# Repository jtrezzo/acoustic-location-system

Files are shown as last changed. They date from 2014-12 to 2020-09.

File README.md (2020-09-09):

acoustic-location-system
========================

Software and hardware designs for an acoustic location system suitable for small underwater ROVs such as OpenROV

This project is about developing an acoustic based location system for small ROVs.

Much of the early work that we have been doing is in the blog: https://forum.openrov.com/t/acoustic-modems-location-and-pingers
That blog covers broader topics, so I wanted to start a forum discussion specifically for developing the acoustic location system.  https://forum.openrov.com/t/acoustic-location-system

Knowing where you are when exploring and gathering images and data is clearly a vital piece of information.  GPS systems provide this on land.  Underwater, radio waves that GPS depends on to function are absorbed by water.  Acoustic signals are one of the best alternatives to transmit information for location and other data communication.  Commercial underwater modem systems exist today and are widely used in exploration, but suitable systems for low-cost small size platforms like OpenROV are not available.  This project plans to deliver such a system and is in-part inspired by university research in this area – Bridget Benson’s UCSD PhD Thesis http://haduken.ucsd.edu/papers/phd-thesis-benson.pdf is one example.
Information about 3D location in real-time is a key enabler for many scientific and exploratory needs. The technology to do this is known, but has not been scaled down for systems of this size. With location information, one could map any discoveries (sunken ships, archeological sites, and coral reefs are some examples). Maps of the ocean/lake/cave can be made with location and sensor information together. Virtual Reality and 3D gaming technology could be used to represent information about an exploration either in real-time (shared over the internet) or archived for many to explore on-line as they study results of explorations.
The technical approach is to use acoustic transmissions (ultrasonic sonar) from known locations on the surface (GPS would be used to maintain location of the sender). The ROV would have a receiver unit on board and can determine the time for the signal to arrive. That information along with depth, temperature and the on-board IMU (gyro, compass, accelerometers) would be used to determine/compute location. Location information would be available to the operator of the ROV and a graphical display could be developed (possibly in conjunction with maps of the bottom if available) to help with navigation.

Current status and near term work items:
Working designs for ultrasonic Power AMP and receiver exist and initial testing with 40KHz piezoelectric transducers has begun.  A micro-controller or processor can be used to generate a 40KHz square wave pulse which is shaped and amplified into a sine wave to drive the transducer.  Currently the amplifier produces a 27Vp-p signal.  If testing shows that this is not enough to generate a powerful enough ultrasonic pulse, a step-up transformer may be required.
The high gain (> 100), high input impedance (FET front end) receiver amplifier design includes a narrow band pass filter to allow only frequencies in the desired range to be amplified.  This receiver needs to be packaged and integrated with the ROV electronics along with a micro-controller to process the waveform (>100 samples/sec and real-time FFT processing required).  
System level: Some how the timing for the start of the pulse from each transmitter (correlated with GPS location at time of transmission) must be matched against the time the first pulse is received (any delayed echoes would be rejected).  The time of travel for the pulse would be used to calculate the distance from the transmitter (with know location) and along with depth information, water temperature, salinity (salt or fresh) and IMU data (plus and location history - dead reckoning, etc.) location would be determined. Data from a second transmitter some distance from the first would greatly help the calculation (see Virtual Long Baseline VLBL Navigation).  The transmissions and calculations should be able to be done every tenth of a second to provide timely location.
I will establish a location on GitHub for this project and start to organize existing material there.  for now, take a look at the blog https://forum.openrov.com/t/acoustic-modems-location-and-pingers.
It would speed things up if I got some help with the micro-controller software while I continue with the electronics and in the water testing.  To do: sample the signal and determine when a 40KHz pulse arrives.  Digital signal processing (DSP) analysis would be the likely approach.  Also will need to determine which micro-controller is adequate to handle this processing load.  I will collect some raw data samples using my NI VirtualBench if someone just wants to work on the DSP part.
There are a few folks already interested, and some possibility of collaboration is there.
If you are interested in getting involved, please let me know and what area(s) you think you can hep with.

I have added a folder with results from acoustic testing.  It includes the results of some initial DSP processing using MATLAB, courtesy of Frikk Solberg of Norway.

Regards,

Jim Trezzo
jtrezzo@trezco.com

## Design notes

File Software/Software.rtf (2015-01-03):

Software folder

TonePulse - simple program to generate pulse of square waves at 40KHz and send digital trigger to data acquisition program (start collecting points). The trigger will be sent down the tether to the micro controller on the ROV. The square wave will be input to the ultrasonic transmitter that drives the transducer. This software will be modified to read the GPS data from a USB GPS device and record time and location when pulse is sent.

adcspeedtest (3.1 and 3.2) - using Teensy 3.1 micro controller, can sample signal at > 250K samples per second. adcspeedtest3.1 uses ADC library (ADC-master) from the Teensy website and collects as many points as can fit into memory. adcspeedtest3.2 uses built in library for Teensy. It only stores 500 points (can be modified to many more) and is triggered by a digital I/O. Both programs are test software for collecting signal data remotely using a micro controller. The plan is to put the analog receiver and Teensy 3.1 into the e-chassis on the ROV and interface with the BBB using the serial port. The transducer will be attached to the ROV and connected to a pair of wires that go into the e-chassis. The analog ultrasonic amplifier will be connected to the ADC on the Teensy. I need to modify the circuit to provide a DC bias and over-voltage protection (ADC only goes from 0-3.3V, the signal is 40KHz AC)

After each cycle of points collection the adcspeedtest program outputs the results as CSV data to the serial port. I then cut and past the results into a text file for processing.

PythonProgram - First cut at reading results from points collection into a graph. This software can evolve to do some DSP analysis. Once the algorithms are figured out (to measure the time for the acoustic pulse to arrive) this can be implemented on the micro controller and time-stamped results can be sent to the BBB (as a JSON string). The OpenROV Node.js software (via a plugin) can send the results as part of the socket.io data stream to software on the surface which can do the calculation for location (surface transmitter has GPS location and time pulse was sent).

First phase of this experiment is to acquire points data from on-board the ROV and modify electronics and software based on observations.

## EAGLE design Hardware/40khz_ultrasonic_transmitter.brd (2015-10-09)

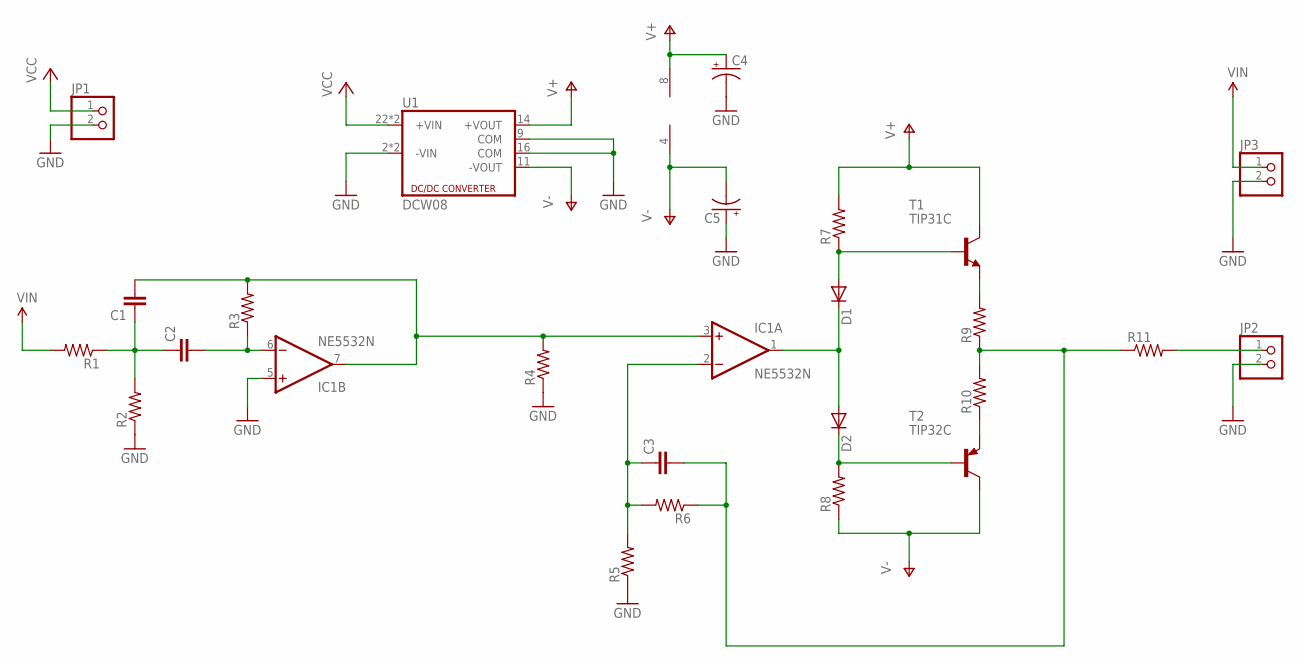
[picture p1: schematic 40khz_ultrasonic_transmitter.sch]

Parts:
C1, C2, C3: CAPPTH2; CAP-PTH-SMALL2
C4, C5: CAP_POLPTH1; CPOL-RADIAL-100UF-25V
D1, D2: DIODE1N4148; DIODE-1N4148
IC1: NE5532N; DIL08
JP1, JP2, JP3: PINHD-1X2; 1X02
R1, R2, R3, R4, R5, R6, R7, R8, R9, R10: RESISTORPTH-1/4W; AXIAL-0.4
R11: RESISTORPTH-2W; AXIAL-0.8
T1: TIP31C; TO220
T2: TIP32C; TO220
U1: DCW08

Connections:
GND: C4.2 (-), C5.1 (+), IC1.5 (+IN), JP1.2, JP2.2, JP3.2, R2.P$1 (1), R4.P$1 (1), R5.P$1 (1), U1.2 (-VIN), U1.3 (-VIN), U1.9 (COM), U1.16 (COM)
unnamed: C3.2, R6.P$1 (1), R9.P$1 (1), R10.P$2 (2), R11.P$1 (1)
unnamed: R9.P$2 (2), T1.3 (E)
unnamed: R10.P$1 (1), T2.3 (E)
unnamed: D1.A, R7.P$1 (1), T1.1 (B)
unnamed: D2.C, R8.P$2 (2), T2.1 (B)
unnamed: C1.2, IC1.3 (+IN), IC1.7 (OUT), R3.P$2 (2), R4.P$2 (2)
unnamed: C1.1, C2.1, R1.P$1 (1), R2.P$2 (2)
unnamed: C3.1, IC1.2 (-IN), R5.P$2 (2), R6.P$2 (2)
unnamed: C2.2, IC1.6 (-IN), R3.P$1 (1)
unnamed: JP2.1, R11.P$2 (2)
unnamed: D1.C, D2.A, IC1.1 (OUT)
V+: C4.1 (+), IC1.8 (V+), R7.P$2 (2), T1.2 (C), U1.14 (+VOUT)
V-: C5.2 (-), IC1.4 (V-), R8.P$1 (1), T2.2 (C), U1.11 (-VOUT)
VCC: JP1.1, U1.22 (+VIN), U1.23 (+VIN)
VIN: JP3.1, R1.P$2 (2)

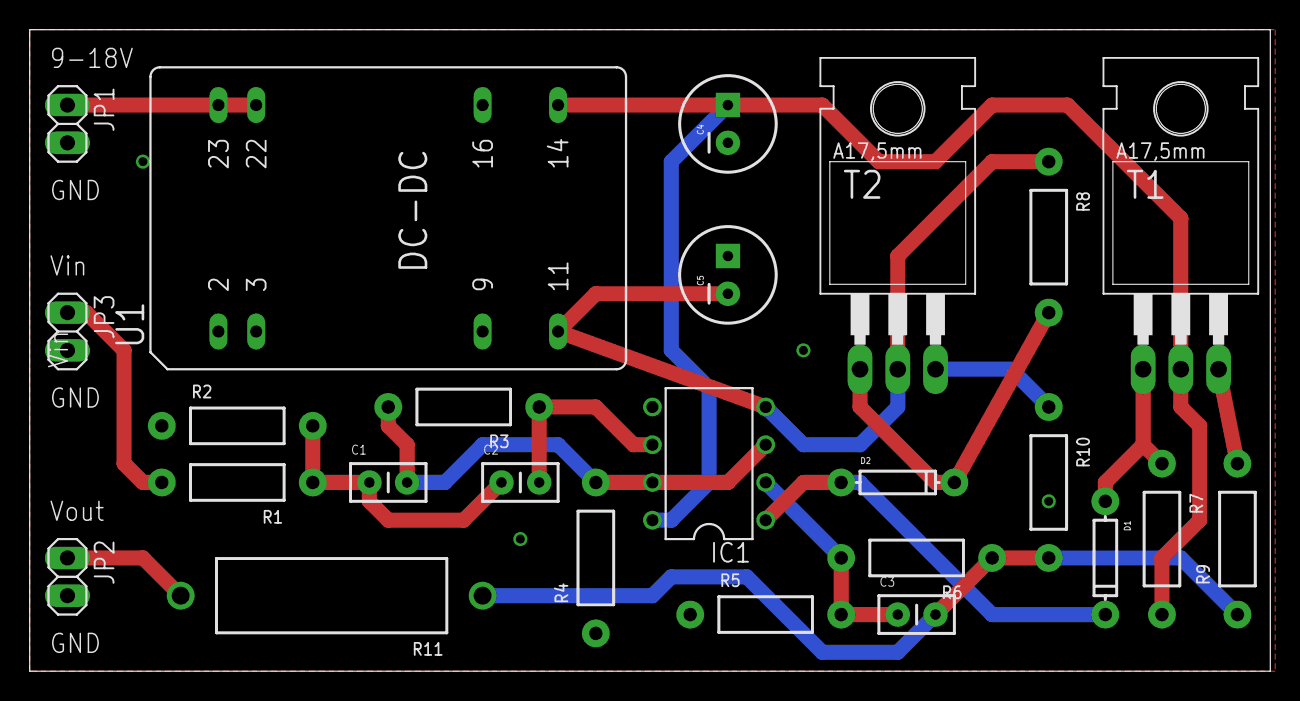
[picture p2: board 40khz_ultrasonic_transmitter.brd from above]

Board: 2 copper layers, 83.5 x 43.2 mm, 25 parts (0 on the bottom side), 16 nets.

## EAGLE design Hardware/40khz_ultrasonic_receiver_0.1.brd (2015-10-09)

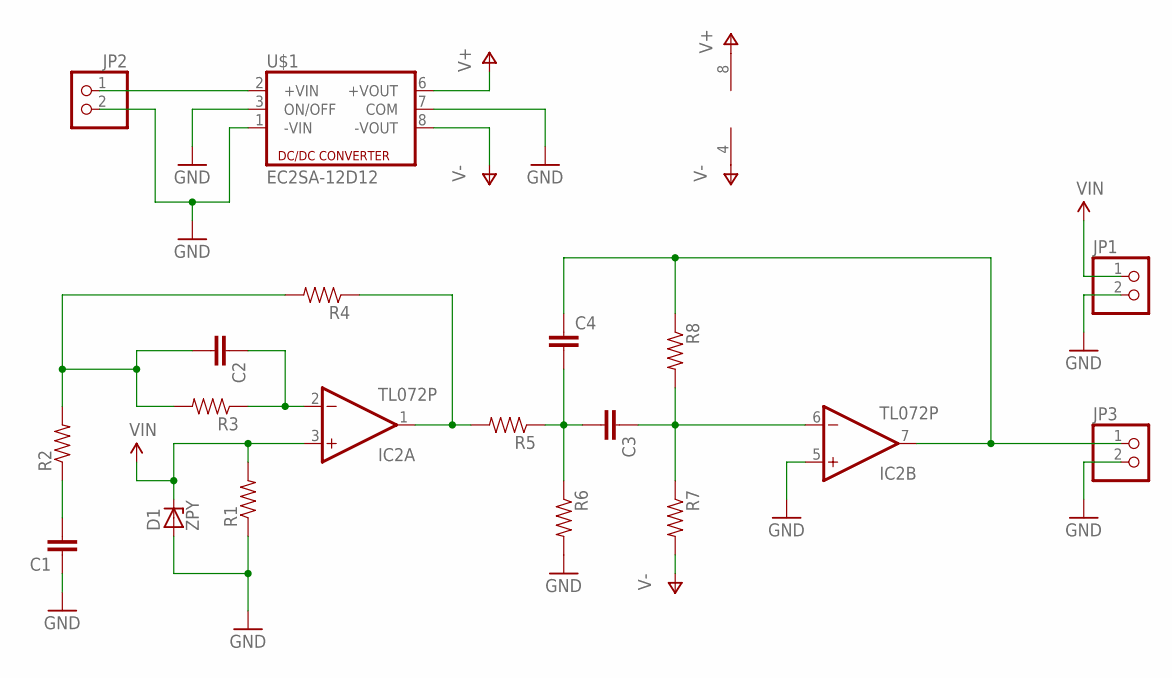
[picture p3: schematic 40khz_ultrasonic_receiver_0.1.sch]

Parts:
C1, C2, C3, C4: CAPPTH; CAP-PTH-SMALL
D1: ZPY; DO41Z10
IC2: TL072P; DIL08
JP1, JP2, JP3: PINHD-1X2; 1X02
R1, R2, R3, R4, R5, R6, R7, R8: RESISTORPTH-1/4W; AXIAL-0.4
U$1: EC2SA-12D12; EC2SA

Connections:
GND: C1.1, D1.A, IC2.5 (+IN), JP1.2, JP2.2, JP3.2, R1.P$1 (1), R6.P$2 (2), U$1.1 (-VIN), U$1.3 (ON/OFF), U$1.7 (COM)
unnamed: IC2.1 (OUT), R4.P$1 (1), R5.P$2 (2)
unnamed: C3.2, C4.2, R5.P$1 (1), R6.P$1 (1)
unnamed: C2.1, IC2.2 (-IN), R3.P$1 (1)
unnamed: C4.1, IC2.7 (OUT), JP3.1, R8.P$1 (1)
unnamed: C2.2, R2.P$2 (2), R3.P$2 (2), R4.P$2 (2)
unnamed: C3.1, IC2.6 (-IN), R7.P$1 (1), R8.P$2 (2)
unnamed: C1.2, R2.P$1 (1)
unnamed: JP2.1, U$1.2 (+VIN)
V+: IC2.8 (V+), U$1.6 (+VOUT)
V-: IC2.4 (V-), R7.P$2 (2), U$1.8 (-VOUT)
VIN: D1.C, IC2.3 (+IN), JP1.1, R1.P$2 (2)

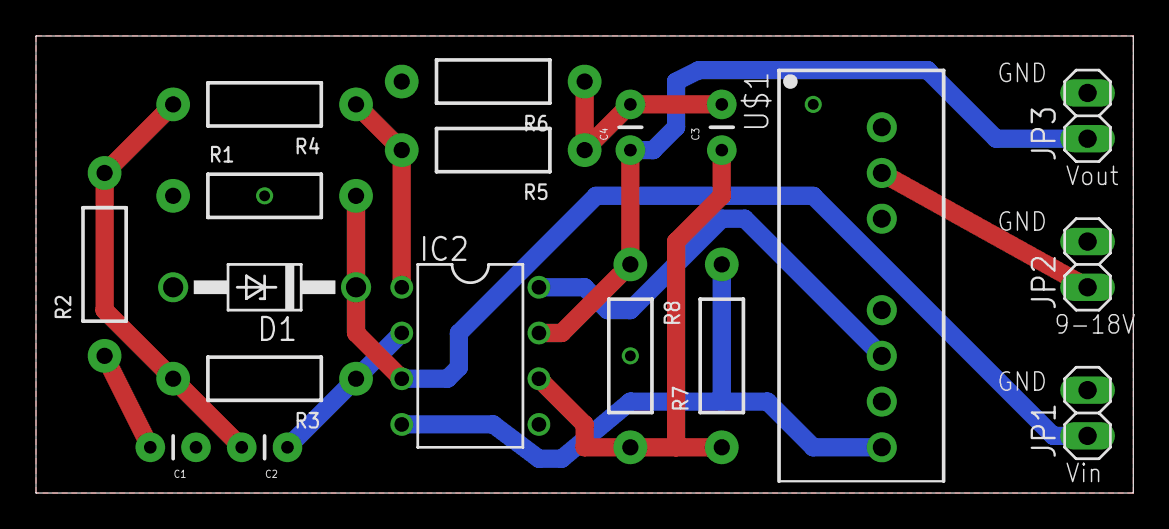
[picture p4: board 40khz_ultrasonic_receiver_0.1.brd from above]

Board: 2 copper layers, 61.0 x 25.4 mm, 18 parts (0 on the bottom side), 12 nets.

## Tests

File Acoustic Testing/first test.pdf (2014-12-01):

First Test of sonar detection algorithm

Here are the first results from the algorithm I have tested. It is quite simple and uses a couple of steps on the received signal

1. Absolute value of received signal
2. Low pass filter it to create an envelope with cutoff frequency at 20kHz
3. Create threshold by finding the average of the signal
4. Find first point where the signal value is larger than the threshold

The filtering procedure works well, but the threshold is not good enough yet. Just averaging is obviously not good enough. I will try to look into some other thresholding methods soon and see what I can do. Underneath are the plots for 0.5m, 1m, 2m, 3m and 4m depth respectively. If it is hard to see, on each figure, the first plot is the sent signal and the second is the received(Or that is what I assume). The third on has the absolute valued version of the received signal in blue, in red is the envelope and the threshold is in green.

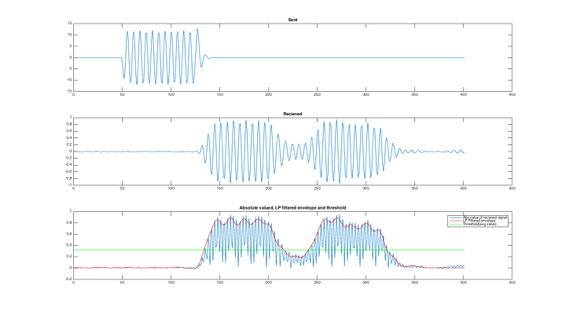
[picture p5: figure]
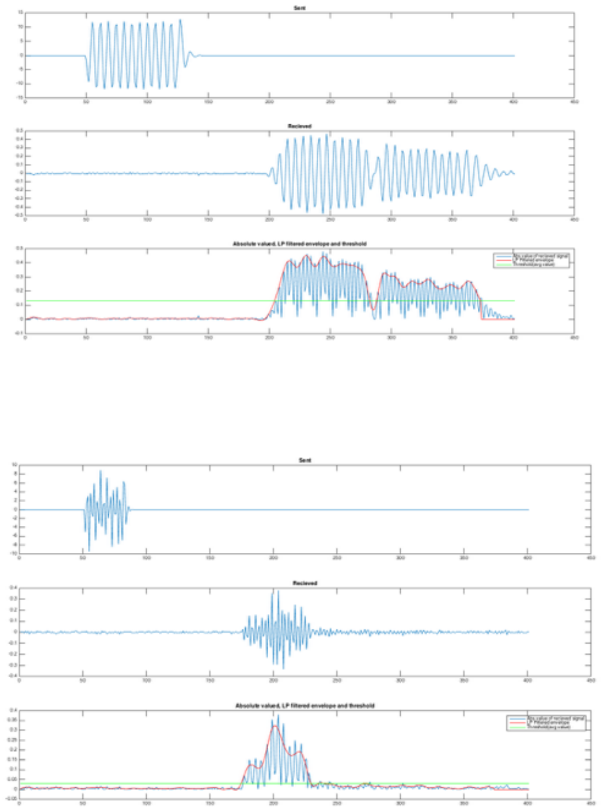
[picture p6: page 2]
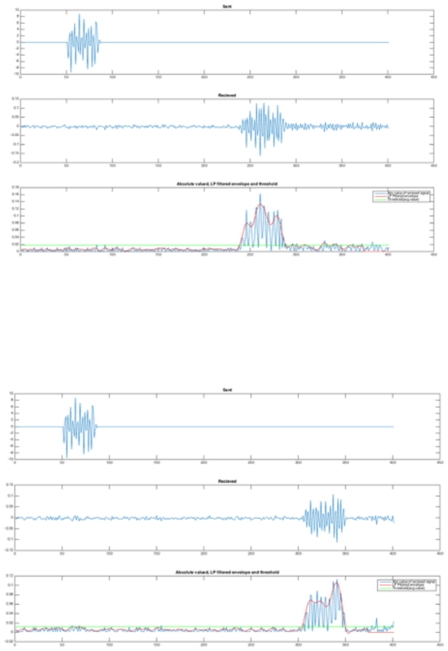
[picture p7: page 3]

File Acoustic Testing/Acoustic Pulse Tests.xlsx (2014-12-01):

Acoustic Pulse Testing |  | 2014-11-06
Distance in Meters | Voltage in mV | Delay in mSec | Meters/Sec
1 | 1860 | 0.68 | 1470.588235
2 | 2290 | 1.35 | 1481.481481
3 | 675 | 2 | 1500
4 | 733 | 2.7 | 1481.481481

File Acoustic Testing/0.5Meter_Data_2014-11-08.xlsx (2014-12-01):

NI VB-8012
Configuration
 | Device
 |  | Name | Serial Number | Firmware
 |  | VB8012-306042E | 306042E | 1.0.1f0
MIXED SIGNAL OSCILLOSCOPE |  |  |  |  |  |  |  |  |  |  |  |  |  |  |  |  |  |  | DC POWER SUPPLY |  |  |  |  |  | DIGITAL MULTIMETER |  |  |  |  |  |  | DIGITAL I/O
Configuration |  |  |  |  |  |  |  |  |  |  |  |  |  |  |  |  |  |  | Configuration |  |  |  |  |  | Configuration |  |  |  |  |  |  | Configuration
 | Analog |  |  |  |  |  |  |  | Trigger |  |  |  |  |  |  |  | Acquisition |  |  | Analog |  |  |  |  |  | Analog |  |  |  |  |  |  | Digital
 |  | Name | Alias | Channel Coupling | Probe Attenuation | Volts Per Division | Vertical Offset (V) | ŒîT (ns) |  | Type | Delay (s) | Reason | Edge | Source | Level (V) | Hysteresis |  | Mode |  |  | Name | Operating Mode | Voltage Set Point | Amperage Set Point |  |  | Name | Measurement Mode | Measurement Range | Input Impedance | Null Offset |  |  | Name | Direction
 |  | 1 | 1 | DC | 1X | 500 mV/ | 0.952537 | 4008 |  | Edge | -2.8e-05 | Triggered | Rising | 2 | 0 | Minimum |  | Peak Detect |  |  | +6 V | CV | 0 | 1 |  |  | DMM | VDC | 100 mV | Normal Impedance (10 MŒ©) | Off |  |  | 0 | Input
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

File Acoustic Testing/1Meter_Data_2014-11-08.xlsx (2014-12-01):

NI VB-8012
Configuration
 | Device
 |  | Name | Serial Number | Firmware
 |  | VB8012-306042E | 306042E | 1.0.1f0
MIXED SIGNAL OSCILLOSCOPE |  |  |  |  |  |  |  |  |  |  |  |  |  |  |  |  |  |  | DC POWER SUPPLY |  |  |  |  |  | DIGITAL MULTIMETER |  |  |  |  |  |  | DIGITAL I/O
Configuration |  |  |  |  |  |  |  |  |  |  |  |  |  |  |  |  |  |  | Configuration |  |  |  |  |  | Configuration |  |  |  |  |  |  | Configuration
 | Analog |  |  |  |  |  |  |  | Trigger |  |  |  |  |  |  |  | Acquisition |  |  | Analog |  |  |  |  |  | Analog |  |  |  |  |  |  | Digital
 |  | Name | Alias | Channel Coupling | Probe Attenuation | Volts Per Division | Vertical Offset (V) | ŒîT (ns) |  | Type | Delay (s) | Reason | Edge | Source | Level (V) | Hysteresis |  | Mode |  |  | Name | Operating Mode | Voltage Set Point | Amperage Set Point |  |  | Name | Measurement Mode | Measurement Range | Input Impedance | Null Offset |  |  | Name | Direction
 |  | 1 | 1 | DC | 1X | 500 mV/ | 1.006228 | 4008 |  | Edge | -2.8e-05 | Triggered | Rising | 2 | 0 | Minimum |  | Peak Detect |  |  | +6 V | CV | 0 | 1 |  |  | DMM | VDC | 100 mV | Normal Impedance (10 MŒ©) | Off |  |  | 0 | Input
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

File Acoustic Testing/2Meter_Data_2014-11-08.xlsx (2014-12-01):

NI VB-8012
Configuration
 | Device
 |  | Name | Serial Number | Firmware
 |  | VB8012-306042E | 306042E | 1.0.1f0
MIXED SIGNAL OSCILLOSCOPE |  |  |  |  |  |  |  |  |  |  |  |  |  |  |  |  |  |  | DC POWER SUPPLY |  |  |  |  |  | DIGITAL MULTIMETER |  |  |  |  |  |  | DIGITAL I/O
Configuration |  |  |  |  |  |  |  |  |  |  |  |  |  |  |  |  |  |  | Configuration |  |  |  |  |  | Configuration |  |  |  |  |  |  | Configuration
 | Analog |  |  |  |  |  |  |  | Trigger |  |  |  |  |  |  |  | Acquisition |  |  | Analog |  |  |  |  |  | Analog |  |  |  |  |  |  | Digital
 |  | Name | Alias | Channel Coupling | Probe Attenuation | Volts Per Division | Vertical Offset (V) | ŒîT (ns) |  | Type | Delay (s) | Reason | Edge | Source | Level (V) | Hysteresis |  | Mode |  |  | Name | Operating Mode | Voltage Set Point | Amperage Set Point |  |  | Name | Measurement Mode | Measurement Range | Input Impedance | Null Offset |  |  | Name | Direction
 |  | 1 | 1 | DC | 1X | 500 mV/ | 0.952537 | 10048 |  | Edge | 0.00087 | Triggered | Rising | 2 | 0 | Minimum |  | Peak Detect |  |  | +6 V | CV | 0 | 1 |  |  | DMM | VDC | 100 mV | Normal Impedance (10 MŒ©) | Off |  |  | 0 | Input
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

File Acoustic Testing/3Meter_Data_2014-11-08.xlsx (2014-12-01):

NI VB-8012
Configuration
 | Device
 |  | Name | Serial Number | Firmware
 |  | VB8012-306042E | 306042E | 1.0.1f0
MIXED SIGNAL OSCILLOSCOPE |  |  |  |  |  |  |  |  |  |  |  |  |  |  |  |  |  |  | DC POWER SUPPLY |  |  |  |  |  | DIGITAL MULTIMETER |  |  |  |  |  |  | DIGITAL I/O
Configuration |  |  |  |  |  |  |  |  |  |  |  |  |  |  |  |  |  |  | Configuration |  |  |  |  |  | Configuration |  |  |  |  |  |  | Configuration
 | Analog |  |  |  |  |  |  |  | Trigger |  |  |  |  |  |  |  | Acquisition |  |  | Analog |  |  |  |  |  | Analog |  |  |  |  |  |  | Digital
 |  | Name | Alias | Channel Coupling | Probe Attenuation | Volts Per Division | Vertical Offset (V) | ŒîT (ns) |  | Type | Delay (s) | Reason | Edge | Source | Level (V) | Hysteresis |  | Mode |  |  | Name | Operating Mode | Voltage Set Point | Amperage Set Point |  |  | Name | Measurement Mode | Measurement Range | Input Impedance | Null Offset |  |  | Name | Direction
 |  | 1 | 1 | DC | 1X | 200 mV/ | 0.381015 | 10048 |  | Edge | 0.00087 | Stop | Rising | 2 | 0 | Minimum |  | Peak Detect |  |  | +6 V | CV | 0 | 1 |  |  | DMM | VDC | 100 mV | Normal Impedance (10 MŒ©) | Off |  |  | 0 | Input
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

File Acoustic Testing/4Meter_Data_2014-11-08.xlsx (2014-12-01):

NI VB-8012
Configuration
 | Device
 |  | Name | Serial Number | Firmware
 |  | VB8012-306042E | 306042E | 1.0.1f0
MIXED SIGNAL OSCILLOSCOPE |  |  |  |  |  |  |  |  |  |  |  |  |  |  |  |  |  |  | DC POWER SUPPLY |  |  |  |  |  | DIGITAL MULTIMETER |  |  |  |  |  |  | DIGITAL I/O
Configuration |  |  |  |  |  |  |  |  |  |  |  |  |  |  |  |  |  |  | Configuration |  |  |  |  |  | Configuration |  |  |  |  |  |  | Configuration
 | Analog |  |  |  |  |  |  |  | Trigger |  |  |  |  |  |  |  | Acquisition |  |  | Analog |  |  |  |  |  | Analog |  |  |  |  |  |  | Digital
 |  | Name | Alias | Channel Coupling | Probe Attenuation | Volts Per Division | Vertical Offset (V) | ŒîT (ns) |  | Type | Delay (s) | Reason | Edge | Source | Level (V) | Hysteresis |  | Mode |  |  | Name | Operating Mode | Voltage Set Point | Amperage Set Point |  |  | Name | Measurement Mode | Measurement Range | Input Impedance | Null Offset |  |  | Name | Direction
 |  | 1 | 1 | DC | 1X | 200 mV/ | 0.381015 | 10048 |  | Edge | 0.00087 | Stop | Rising | 2 | 0 | Minimum |  | Peak Detect |  |  | +6 V | CV | 0 | 1 |  |  | DMM | VDC | 100 mV | Normal Impedance (10 MŒ©) | Off |  |  | 0 | Input
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

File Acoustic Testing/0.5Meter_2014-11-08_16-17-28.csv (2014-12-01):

NI VB-8012
Configuration
 | Device
 |  | Name | Serial Number | Firmware
 |  | VB8012-306042E | 306042E | 1.0.1f0
MIXED SIGNAL OSCILLOSCOPE |  |  |  |  |  |  |  |  |  |  |  |  |  |  |  |  |  |  | DC POWER SUPPLY |  |  |  |  |  | DIGITAL MULTIMETER |  |  |  |  |  |  | DIGITAL I/O
Configuration |  |  |  |  |  |  |  |  |  |  |  |  |  |  |  |  |  |  | Configuration |  |  |  |  |  | Configuration |  |  |  |  |  |  | Configuration
 | Analog |  |  |  |  |  |  |  | Trigger |  |  |  |  |  |  |  | Acquisition |  |  | Analog |  |  |  |  |  | Analog |  |  |  |  |  |  | Digital
 |  | Name | Alias | Channel Coupling | Probe Attenuation | Volts Per Division | Vertical Offset (V) | ΔT (ns) |  | Type | Delay (s) | Reason | Edge | Source | Level (V) | Hysteresis |  | Mode |  |  | Name | Operating Mode | Voltage Set Point | Amperage Set Point |  |  | Name | Measurement Mode | Measurement Range | Input Impedance | Null Offset |  |  | Name | Direction
 |  | 1 | 1 | DC | 1X | 500 mV/ | 0.952537 | 4008.0000 |  | Edge | -00.000028 | Triggered | Rising | 2 | 0.00 | Minimum |  | Peak Detect |  |  | +6 V | CV | 0.000 | 1.000 |  |  | DMM | VDC | 100 mV | Normal Impedance (10 MΩ) | Off |  |  | 0 | Input
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

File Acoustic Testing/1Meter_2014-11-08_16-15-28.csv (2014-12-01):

NI VB-8012
Configuration
 | Device
 |  | Name | Serial Number | Firmware
 |  | VB8012-306042E | 306042E | 1.0.1f0
MIXED SIGNAL OSCILLOSCOPE |  |  |  |  |  |  |  |  |  |  |  |  |  |  |  |  |  |  | DC POWER SUPPLY |  |  |  |  |  | DIGITAL MULTIMETER |  |  |  |  |  |  | DIGITAL I/O
Configuration |  |  |  |  |  |  |  |  |  |  |  |  |  |  |  |  |  |  | Configuration |  |  |  |  |  | Configuration |  |  |  |  |  |  | Configuration
 | Analog |  |  |  |  |  |  |  | Trigger |  |  |  |  |  |  |  | Acquisition |  |  | Analog |  |  |  |  |  | Analog |  |  |  |  |  |  | Digital
 |  | Name | Alias | Channel Coupling | Probe Attenuation | Volts Per Division | Vertical Offset (V) | ΔT (ns) |  | Type | Delay (s) | Reason | Edge | Source | Level (V) | Hysteresis |  | Mode |  |  | Name | Operating Mode | Voltage Set Point | Amperage Set Point |  |  | Name | Measurement Mode | Measurement Range | Input Impedance | Null Offset |  |  | Name | Direction
 |  | 1 | 1 | DC | 1X | 500 mV/ | 1.006228 | 4008.0000 |  | Edge | -00.000028 | Triggered | Rising | 2 | 0.00 | Minimum |  | Peak Detect |  |  | +6 V | CV | 0.000 | 1.000 |  |  | DMM | VDC | 100 mV | Normal Impedance (10 MΩ) | Off |  |  | 0 | Input
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

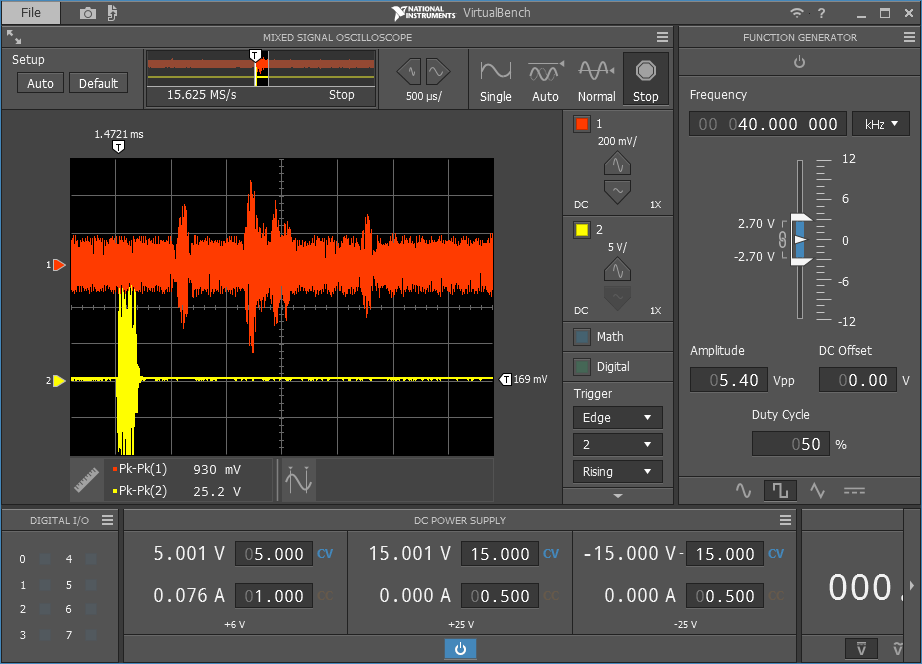
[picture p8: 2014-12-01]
Acoustic Testing/AtBoat1Meter_2014-11-15_16-49-37.png

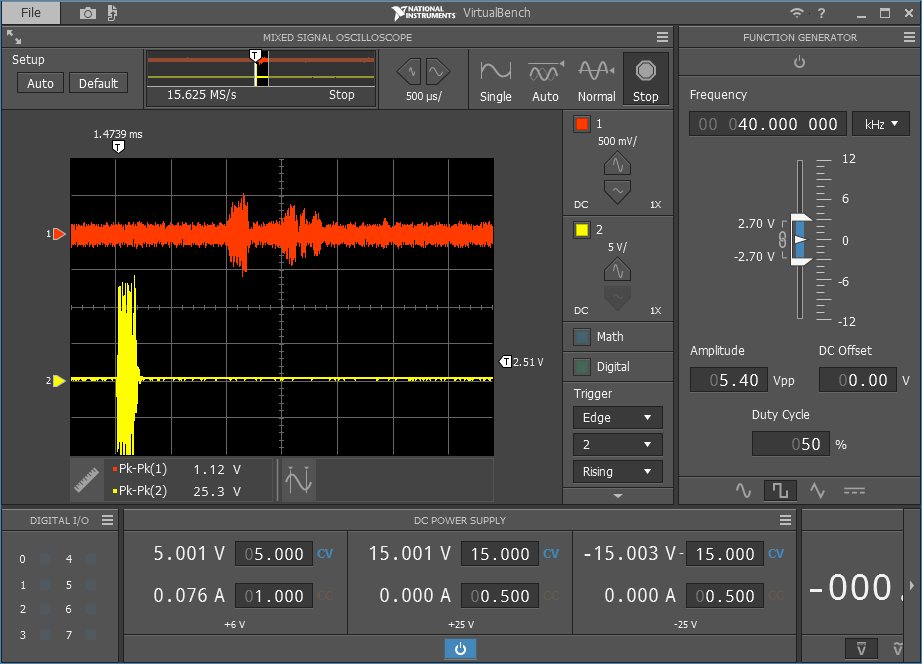
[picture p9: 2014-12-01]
Acoustic Testing/AtBoat4Feet1Mdeep2_2014-11-15_16-32-34.png

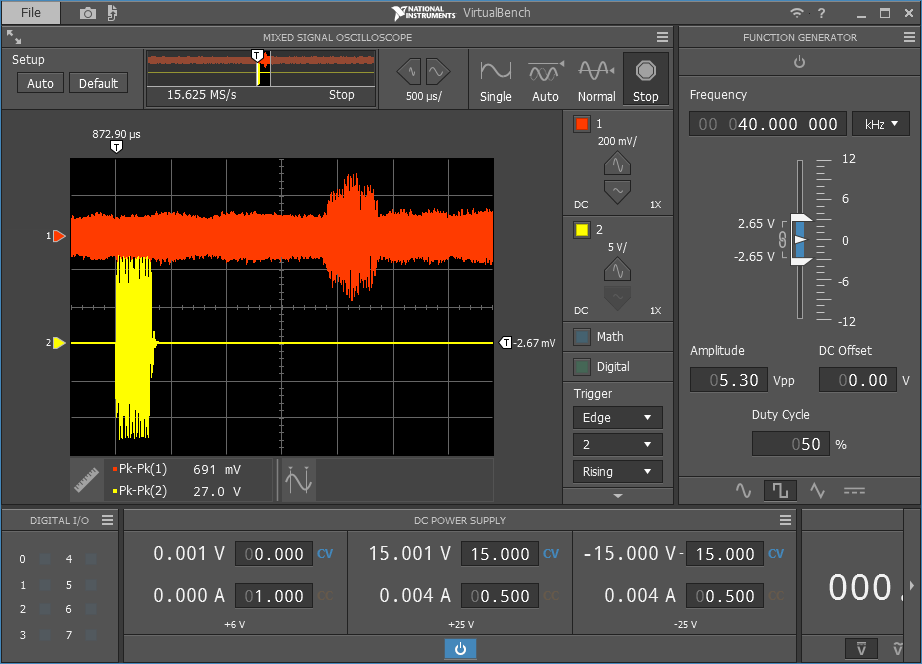
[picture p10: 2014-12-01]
Acoustic Testing/3Meter_2014-11-08_16-21-58.png

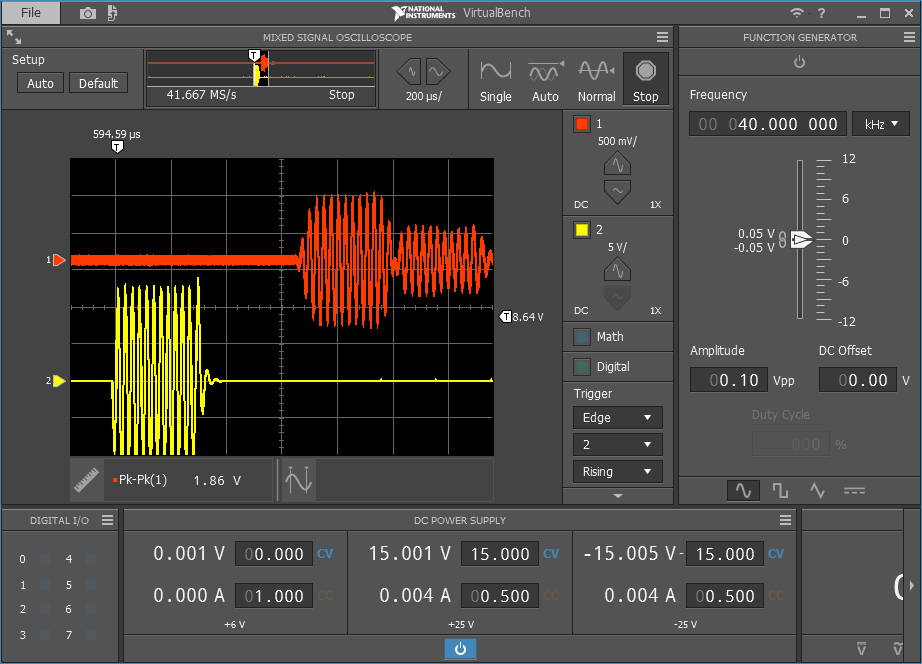
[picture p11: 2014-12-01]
Acoustic Testing/1Meter_2014-11-06_14-54-59.png

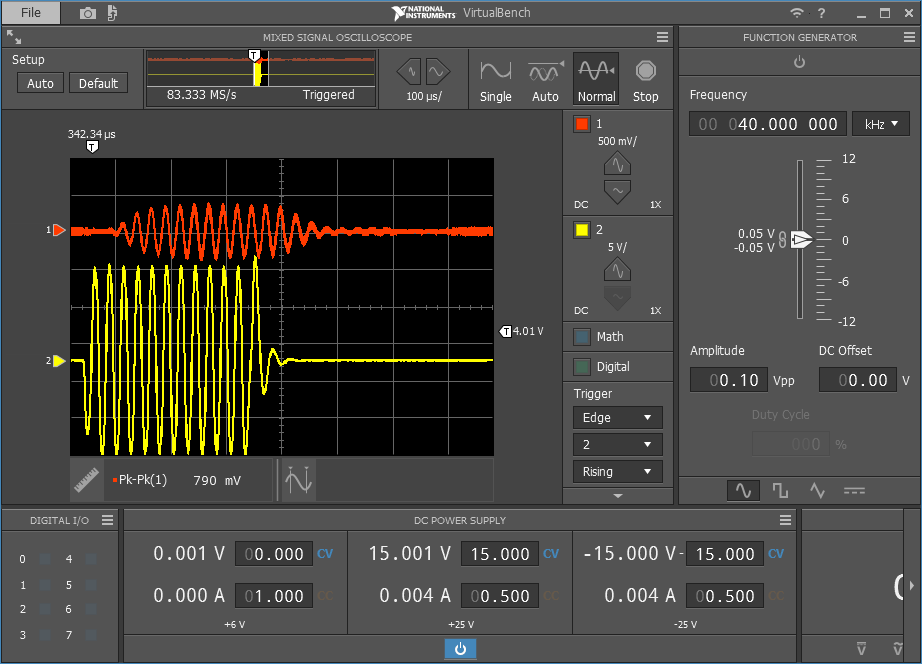
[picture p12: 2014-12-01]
Acoustic Testing/0 Meters_2014-11-04_17-11-12.png

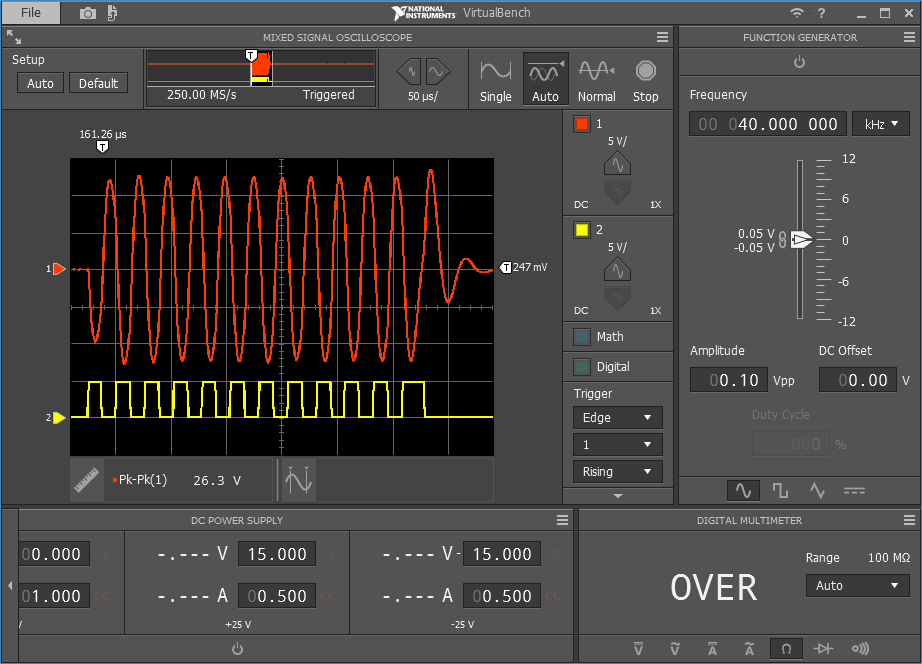
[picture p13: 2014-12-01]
Acoustic Testing/Output From TTL_2014-11-04_13-06-28.png

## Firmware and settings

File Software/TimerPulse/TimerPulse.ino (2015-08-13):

/* Blink using timer1 and send squarewave pulse for specified duration
 
 Turns on and off the on-board LED attached to pin 13,
 using timer1 as specified by "interval"
 Squarewave pulse sent every two intervals for "numCycles" on pin "squareWaveOutPin".
 Trigger sent (high to low for 1 usec) on pin "triggerOutPin" to start external points collection via DAQ
 
*/

#include <TimerOne.h>

// constants won't change. Used here to 
// set pin numbers:
const int ledPin =  13;      // the number of the LED pin

const int triggerOutPin =  8;      // the number of the trigger signal pin
const int squareWaveOutPin = 9; // output pin for square wave pulse
const int frequency = 38700;    // 40KHz - not used at the moment, instead Timer1.initialize() sets 1/2 cycle duration

// Variables will change:
int ledState = LOW;             // ledState used to set the LED


// the follow variable is a long because the time, measured in miliseconds,
// will quickly become a bigger number than can be stored in an int.
long previousMillis = 0;        // will store last time LED was updated
long interval = 1000;           // interval at which to blink (milliseconds)
                                // new cycle starts after two intervals


// Uses the timer interrupt to send a square wave pulse
// shares variables (declared as "volatile") between
// the interrupt service routine and the main program.

void setup() {
  // set the digital pins as output:
  pinMode(ledPin, OUTPUT);
  pinMode(squareWaveOutPin, OUTPUT);
  pinMode(triggerOutPin, OUTPUT);
  // init trigger to HIGH - waiting to sample analog signal on Teensy 3.1
  // High to Low signals start of new sampling cycle
  digitalWrite(triggerOutPin, HIGH);
  
  Timer1.initialize(13);
  Timer1.attachInterrupt(sendPulse); // sendPulse to run every 13 useconds (half of a cycle, approx 38.5KHz)

}

// The interrupt will send a pulse (alternating square wave state), and keep
// track of how many pulses were sent
volatile int pulseState = LOW;
volatile unsigned int cycleCount = 0;    // use volatile for shared variables
volatile unsigned int numCycles = 6;     // pulse duration is numCycles of square wave
volatile boolean  pulse = false;         // send pulse only when true

void sendPulse(void)  //  interrupt service routine
{
  if (pulse == true) {
    if (pulseState == LOW) {
      pulseState = HIGH;
      digitalWrite(squareWaveOutPin, pulseState);
      }
    else {
      pulseState = LOW;
      digitalWrite(squareWaveOutPin, pulseState);
      cycleCount++;                   // increase after each complete square wave sent
      if (cycleCount == numCycles) {  // check to see if we have sent required number of cycles
        pulse = false;                // set false when pulse cycles completed
        cycleCount = 0;        
        }
      }
    }
}


void loop()
{
  // here is where you'd put code that needs to be running all the time.

  
  // check to see if it's time to blink the LED; that is, if the 
  // difference between the current time and last time you blinked 
  // the LED is bigger than the interval at which you want to 
  // blink the LED.
  unsigned long currentMillis = millis();
 
  if(currentMillis - previousMillis > interval) {  // blink led
    // save the last time you blinked the LED 
    previousMillis = currentMillis;
    

    // if the LED is off turn it on and vice-versa:
    if (ledState == LOW) {        // start a new cycle
      ledState = HIGH;

      // toggle trigger to start sampling analog signal on Teensy 3.1
      digitalWrite(triggerOutPin, LOW);

  // to read a variable which the interrupt code writes, we
  // must temporarily disable interrupts, to be sure it will
  // not change while we are reading.  To minimize the time
  // with interrupts off, just quickly make a copy, and then
  // use the copy while allowing the interrupt to keep working.

      noInterrupts();
      pulse = true;    // start sending new pulse cycles
      interrupts();

      // reset trigger to HIGH - waiting to sample analog signal on Teensy 3.1
      digitalWrite(triggerOutPin, HIGH);

      }
    
      else {
        ledState = LOW;
      }
      
      // set the LED with the ledState of the variable:
      digitalWrite(ledPin, ledState);
  }
}

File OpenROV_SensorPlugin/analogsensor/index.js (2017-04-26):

(function() {
  const Listener = require('Listener');
  const fs = require('fs');
  const path = require('path');
  
  const SerialPort = require('serialport'); // modified code from SerialBridge.js
  var EventEmitter = require('events').EventEmitter;
  var logger = require('AppFramework.js').logger;



  var reader = new StatusReader();

  class AnalogSensor {
    constructor(name, deps) {
      deps.logger.debug('AnalogSensor plugin loaded');
      console.log('AnalogSensor plugin loaded');

      this.globalBus = deps.globalEventLoop; // This is the server-side messaging bus. The MCU sends messages to server plugins over this
      this.cockpitBus = deps.cockpit; // This is the server<->client messaging bus. This is how the server talks to the browser

      this.hasSaidHello = false;
      
      //By defaulting, we will get zero values in the file saves if we are not actually getting these messages
      this.depth = 0;
      this.temp = 0;

      var self = this;

      // Pre-define all of the event listeners here. We defer enabling them until later.
      // Look at src/libs/Listener.js to see how these work.
      this.listeners = {
        // Listener for Settings updates
        settings: new Listener(self.globalBus, 'settings-change.analogsensor', true, function(settings) {
          // Apply settings
          self.settings = settings.analogsensor;

          // Emit settings update to cockpit
          self.cockpitBus.emit('plugin.analogsensor.settingsChange', self.settings);
        }),

        // Listener for MCU status messages
        mcuStatus: new Listener(self.globalBus, 'mcu.status', false, function(data) {
          // Check for the analogsensor field name in the MCU's status update
          if ('analogsensor' in data) {
            // Get the message that the MCU sent to us
            var message = data.analogsensor;

            // Re-emit the message on the cockpit messaging bus (talks to the browser)
            self.cockpitBus.emit('plugin.analogsensor.message', message);
          }
          
          if ('temp' in data){ //Assuming "temp" is right, it might be all caps.
            self.temp = data.temp;
          }
        }),
        
        depthStatus: new Listener(self.globalBus, 'plugin.diveProfile.depth', false, function(value){
          self.depth = value;
        }),

        sayHello: new Listener(self.cockpitBus, 'plugin.analogsensor.sayHello', false, function(powerIn) {
          var command;

          // Create a command in the format "command( parameters )"
          if (self.hasSaidHello) {
            command = 'ex_hello(' + 0 + ')';
            self.hasSaidHello = false;
          } else {
            command = 'ex_hello(' + 1 + ')';
            self.hasSaidHello = true;
          }

          // Send command to mcu
          self.globalBus.emit('mcu.SendCommand', command);
        })
      }
    }

    // This is automatically called when cockpit loads all of the plugins, and when a plugin is enabled
    start() {
      // Enable the listeners!
      this.listeners.settings.enable();
      this.listeners.mcuStatus.enable();
      this.listeners.sayHello.enable();
      this.listeners.depthStatus.enable();
      var self = this;
      var ticks = 0;

      SerialPort.list(function(err, ports) {
        ports.forEach(function(port) {
          console.log(port.comName);
        });
      });

      var uartPath = "/dev/ttyACM0" // from SerialBridge.js
      var uartBaud = 115200;

      const serialPort = new SerialPort(uartPath, {
        baudRate: uartBaud,
        //            parser: SerialPort.parsers.ReadLine('\r\n'),  // dosen't work on serialPort 5.x
        autoOpen: false
      });

      serialPort.open(function(err) {
        if (err) {
          return console.log('Error opening port: ', err.message);
        }
      });

      serialPort.flush(function(err) {
        //  setTimeout(function () {
        //    sp.close(function (err) {
        //    });
        //  }, 10);
        console.log('Serial port flushed');
      });


      var Readline;
      var parser;

      if (SerialPort.parsers.Readline) {
        Readline= SerialPort.parsers.Readline; 
        parser=serialPort.pipe(Readline({delimiter: '\r\n'}));
        console.log('Readline');
      }
      if (SerialPort.parsers.ReadLine) {        // This one for serialPort 5.x
        Readline = SerialPort.parsers.ReadLine;
        parser = serialPort.pipe(Readline({
          delimiter: '\r\n'
        }));
        console.log('ReadLine');
      }
        if (SerialPort.parsers.readline) {
        Readline= SerialPort.parsers.readline; 
        parser=serialPort.pipe(Readline({delimiter: '\r\n'}));
        console.log('readline');
      }


      serialPort.on('open', function() {
        // logger.debug('Serial port opened');
        console.log('Serial port opened');
        serialPort.write('b');              //  signal microcontroller to start "b" for begin
        console.log('wrote b');
      });

      parser.on('data', function(jsondata) {
        console.log('Got data');
        var data
        try{
          data = JSON.parse(jsondata);
          
          if (data.Group){
            var filename = "sd_" + Date.now() + ".json"
            var sampleSet = {}
            sampleSet.group = data;
            sampleSet.depth = self.depth;
            sampleSet.temp = self.temp;
            fs.appendFile(path.join("/usr/share/cockpit/analogsensor",filename),JSON.stringify(sampleSet));
          }
          
          console.dir(data);
          console.log("Group=",data.Group)
          if (data.Group == 50){
            serialPort.write('b');              //  signal microcontroller to start "b" for begin
            console.log('wrote b');            
          }
        }catch(e){
          //ignore data, not valid json
          
          console.warn("Bad json found from serial port", jsondata);
        }
        //console.log(data.ToString())
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

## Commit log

2014-12-01 adding acoustic test data
    [0.5Meter_2014-11-08_16-17-28.csv, 0.5Meter_Data_2014-11-08.xlsx, 1Meter_2014-11-08_16-15-28.csv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]
2015-06-22 Added dsp_analysis with filter evaluation
2015-08-13 added updated version of adcspeedtest (v3.3) and new TimerPulse program
    adcspeedtest3.3 was rewritten to use a hardware timer interrupt to
    control the sampling rate better. Runs on the teensy 3.1 micro
    controller.
    TimerPulse is a new version of the arduino pulse signal generator.
    This replaces TonePulse and uses timer interrupts for more direct
    control than Tone() allowed.
    [TimerPulse.ino, adcspeedtest3.3.ino]
2015-10-08 Created Rev 0.1 and fixed op-amp wiring
    [40khz_ultrasonic_receiver_0.1.brd, 40khz_ultrasonic_receiver_0.1.sch]
2015-10-08 Added PCB files
    [40khz_ultrasonic_receiver.brd, 40khz_ultrasonic_receiver.sch, 40khz_ultrasonic_receiver_0.1.brd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]
2017-04-26 Create folder for OpenROV Sensor Plugin
    Create folder for development work on plugin to allow acoustic sensor
    system (based on micro controller sub-system) to inter-operate with
    OpenROV Node JS based plug-in components
2017-04-26 Added analog sensor plug-in code
    Added folder “analog sensor” with latest under-development code

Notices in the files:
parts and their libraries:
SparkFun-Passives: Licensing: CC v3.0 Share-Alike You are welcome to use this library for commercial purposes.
